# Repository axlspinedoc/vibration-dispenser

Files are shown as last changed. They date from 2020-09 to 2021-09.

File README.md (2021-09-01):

<h3 align="center">Dispensador Vibratorio</h3>

<div align="center">

[]()

</div>

---

<p align="center"> Automatización de un equipo dispensador de alimentos a granel
    <br> 
</p>

# 🧐 Acerca del proyecto 

Este repositorio contiene el código fuente del sistema operativo de una dispensador a granel utilizando un microcontrolador Amega2560

# 🏁 Preparación necesaria 

1. Instale la herramienta [VSCode](https://code.visualstudio.com)

2. Abra el programa y entre a _File_, _Preferences_, _Extensions_.

3. En el buscador, introduzca _C/C++_ e instale la extensión.

4. Nuevamente en el buscador, introduzca ahora _PlatformIO IDE_ e instale.

5. Una vez instalados correctamente, cada vez que abra VSCode aparecerá la pantalla de inicio con el anuncio "Welcome to PlatformIO"

6. Descargue una copia de este repositorio desde la opción _Code_, _Descargar Zip_. Descomprima en una ubicación conocida.

7. Desde la pestaña de _home_ de PlatformIO, seleccione _import Arduino project_

8. El programa cargara el proyecto y actualizará los documentos dependiendo la computadora donde se abra. *Espere 5 minutos*, esto permitirá que esté listo para programar

9. Para verificar que está listo busque el botón _Build_ en la barra inferior azul, marcado con el símbolo de palomilla

10. Si en el panel inferior aparece la instrucción [SUCCESS], está listo para programar. Conecte el Arduino a su computadora con el cable USB

11. Presione el botón _Upload_ en la barra inferior azul, marcado con una flecha hacia la derecha. Este botón está inmediatamente a la derecha del botón con la palomilla.

12. Pasados 15 segundos, el _Arduino_ se habrá reinicializado. ¡Ha actualizado exitosamente su microcontrolador!

# Para realizar Ajustes

Abra el archivo _utilities.h_ dentro de la carpeta _lib/inc_

Desde aquí puede editarse:

1. Producto a cargar al iniciar el equipo
2. Peso inicial default
3. Tiempo de espera cuando termina de vaciarse la Tolva
4. Selección del modo del relevador
5. Posiciones de la puerta en el estado ABIERTO y CERRADO
6. Sensibilidad de la báscula durante dispensado y vaciado
7. Calibración de báscula
8. Tiempo de señal de _Relay_
9. Tiempo de espera después de dispensar en tolva

Para editar la base de datos de productos abra el archivo _productos.h_ dentro de la carpeta _lib/inc_

Siga las indicaciones del archivo para agregar productos seleccionables desde la pantalla

# ⛏️ Built Using 

- [Visual Studio Code](https://code.visualstudio.com) - IDE
- [PlatformIO](https://platformio.org) - Embedded development IDE
- [Arduino Mega](https://www.arduino.cc) - Prototyping

# ✍️ Authors 

- [@axlspinedoc](https://github.com/axlspinedoc) - Developer

# 🎉 Acknowledgements 

- Amber Macias

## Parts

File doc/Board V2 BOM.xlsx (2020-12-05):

Costo de material por unidad | $938.00
Elemento | Cantidad | Costo Unitario | Costo final | Link
Pantalla LCD 16x2 | 1 | $60.00 | $60.00 | https://troxino.com/collections/pantallas/products/pantalla-lcd-caracteres-16x2-fondo-azul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
Arduino Mega genérico | 1 | $325.00 | $325.00 | https://troxino.com/products/arduino-mega-2560-generico?_pos=2&_sid=26eb9a378&_ss=r
Manufactura PCB | 1 | $68.00 | $68.00 | https://jlcpcb.com
Módulo 4 Relays | 1 | $70.00 | $70.00 | https://troxino.com/products/modulo-de-relevadores-4-canales-5v?_pos=4&_sid=eee105e99&_ss=r
Adaptor I2C para LCD | 1 | $45.00 | $45.00 | https://troxino.com/products/pantalla-lcd-caracteres-16x2-con-interfaz-i2c-integrada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
Tira sencilla 36 Pines | 2 | $8.00 | $16.00 | https://www.steren.com.mx/tira-sencilla-de-36-pines-para-circuitos-impresos.html
Regulador 5V para Servo | 1 | $9.00 | $9.00 | https://www.steren.com.mx/regulador-de-voltaje-positivo-5v-1a.html
Capacitor electrolítico 2.2uF | 2 | $3.00 | $6.00 | https://www.steren.com.mx/capacitor-electrolitico-radial-de-2-2-uf-micro-faradios-a-63-volts.html
Paquete de 10 resistencias 10K ohms | 1 | $10.00 | $10.00 | https://troxino.com/collections/resistencias/products/10-resistencias-4-7k-ohms-1-4-watts-1
Módulo driver para motor DC LD298 | 1 | $65.00 | $65.00 | https://troxino.com/products/puente-h-doble-l298n?variant=17821544415332
Servo Motor MG995 | 1 | $110.00 | $110.00 | https://troxino.com/products/servomotor-mg995?_pos=1&_sid=a9c5e8dc2&_ss=r
Boton pulsador rojo | 7 | $22.00 | $154.00 | http://semty.mx/index.php?id_product=867&controller=product
Regulador 120VAC a 12VD | 1 | $0.00 | $0.00
Header con clavija x2 pines | 2 | $0.00 | $0.00
Header con clavija x3 pines | 5 | $0.00 | $0.00
Header con clavija x4 pines | 4 | $0.00 | $0.00

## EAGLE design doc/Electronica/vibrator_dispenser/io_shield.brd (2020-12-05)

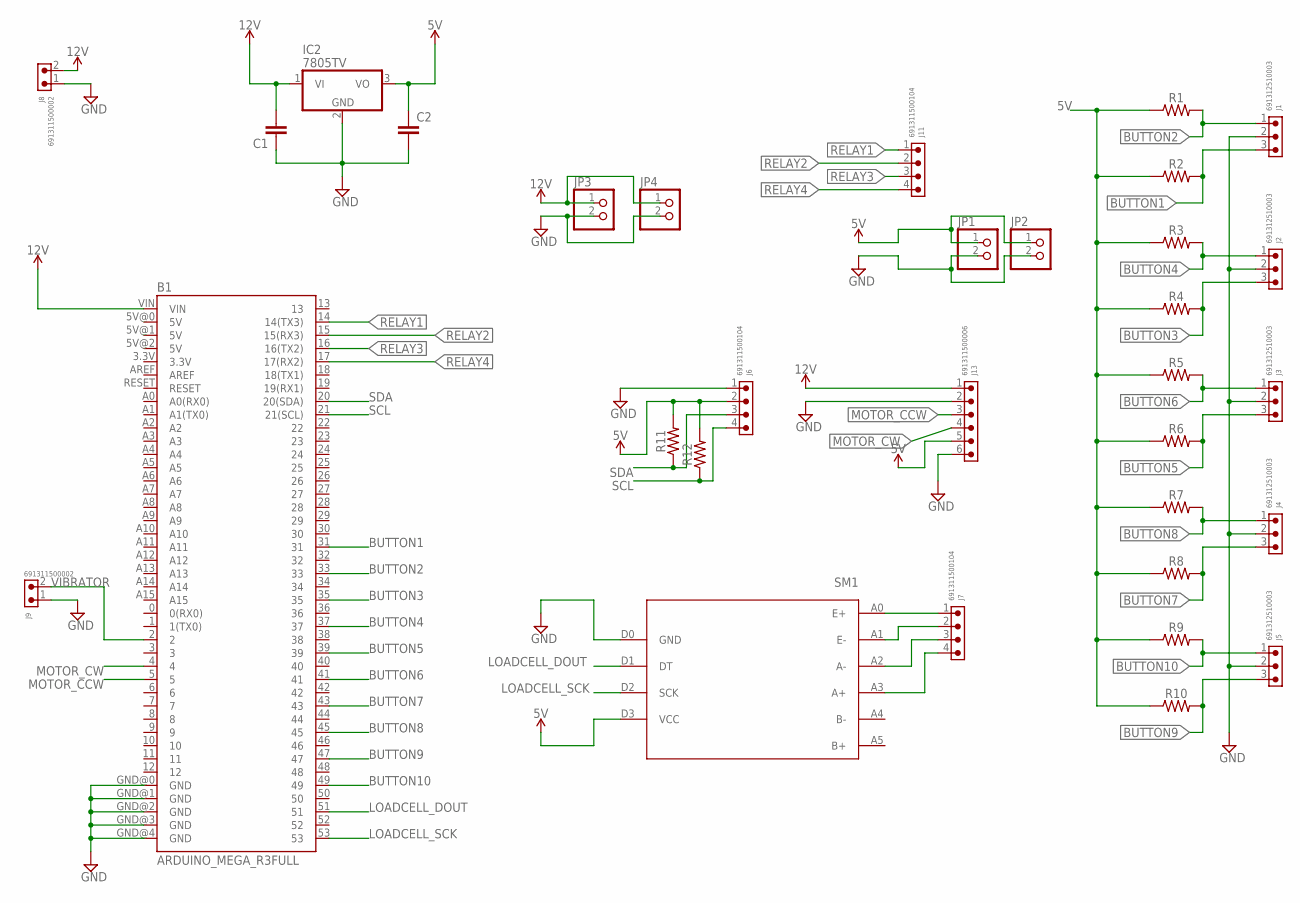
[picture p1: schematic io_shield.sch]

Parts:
B1: ARDUINO_MEGA_R3FULL; ARDUINO_MEGA
C1, C2: C-EU050-025X075; C050-025X075
IC2: 7805TV; TO220V
J1, J2, J3, J4, J5: 691312510003
J6, J7, J11: 691311500104
J8, J9: 691311500002
J13: 691311500006
JP1, JP2, JP3, JP4: PINHD-1X2; 1X02
R1, R2, R3, R4, R5, R6, R7, R8, R9, R10, R11, R12: AXIAL-0.3
SM1: HX711

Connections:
5V: C2.1, IC2.3 (VO), J6.2, J13.5, JP1.1, JP2.1, R1.P$1 (1), R2.P$1 (1), R3.P$1 (1), R4.P$1 (1), R5.P$1 (1), R6.P$1 (1), R7.P$1 (1), R8.P$1 (1), R9.P$1 (1), R10.P$1 (1), R11.P$2 (2), R12.P$2 (2), SM1.D3 (VCC)
12V: B1.VIN, C1.2, IC2.1 (VI), J8.2, J13.1, JP3.1, JP4.1
A+: J7.4, SM1.A3 (A+)
A-: J7.3, SM1.A2 (A-)
BUTTON1: B1.31, J1.3, R2.P$2 (2)
BUTTON2: B1.33, J1.1, R1.P$2 (2)
BUTTON3: B1.35, J2.3, R4.P$2 (2)
BUTTON4: B1.37, J2.1, R3.P$2 (2)
BUTTON5: B1.39, J3.3, R6.P$2 (2)
BUTTON6: B1.41, J3.1, R5.P$2 (2)
BUTTON7: B1.43, J4.3, R8.P$2 (2)
BUTTON8: B1.45, J4.1, R7.P$2 (2)
BUTTON9: B1.47, J5.3, R10.P$2 (2)
BUTTON10: B1.49, J5.1, R9.P$2 (2)
E+: J7.1, SM1.A0 (E+)
E-: J7.2, SM1.A1 (E-)
GND: B1.GND@0 (GND), B1.GND@1 (GND), B1.GND@2 (GND), B1.GND@3 (GND), B1.GND@4 (GND), C1.1, C2.2, IC2.2 (GND), J1.2, J2.2, J3.2, J4.2, J5.2, J6.1, J8.1, J9.1, J13.2, J13.6, JP1.2, JP2.2, JP3.2, JP4.2, SM1.D0 (GND)
LOADCELL_DOUT: B1.51, SM1.D1 (DT)
LOADCELL_SCK: B1.53, SM1.D2 (SCK)
MOTOR_CCW: B1.5, J13.3
MOTOR_CW: B1.4, J13.4
RELAY1: B1.14 (14(TX3)), J11.1
RELAY2: B1.15 (15(RX3)), J11.2
RELAY3: B1.16 (16(TX2)), J11.3
RELAY4: B1.17 (17(RX2)), J11.4
SCL: B1.21 (21(SCL)), J6.4, R12.P$1 (1)
SDA: B1.20 (20(SDA)), J6.3, R11.P$1 (1)
VIBRATOR: B1.2, J9.2

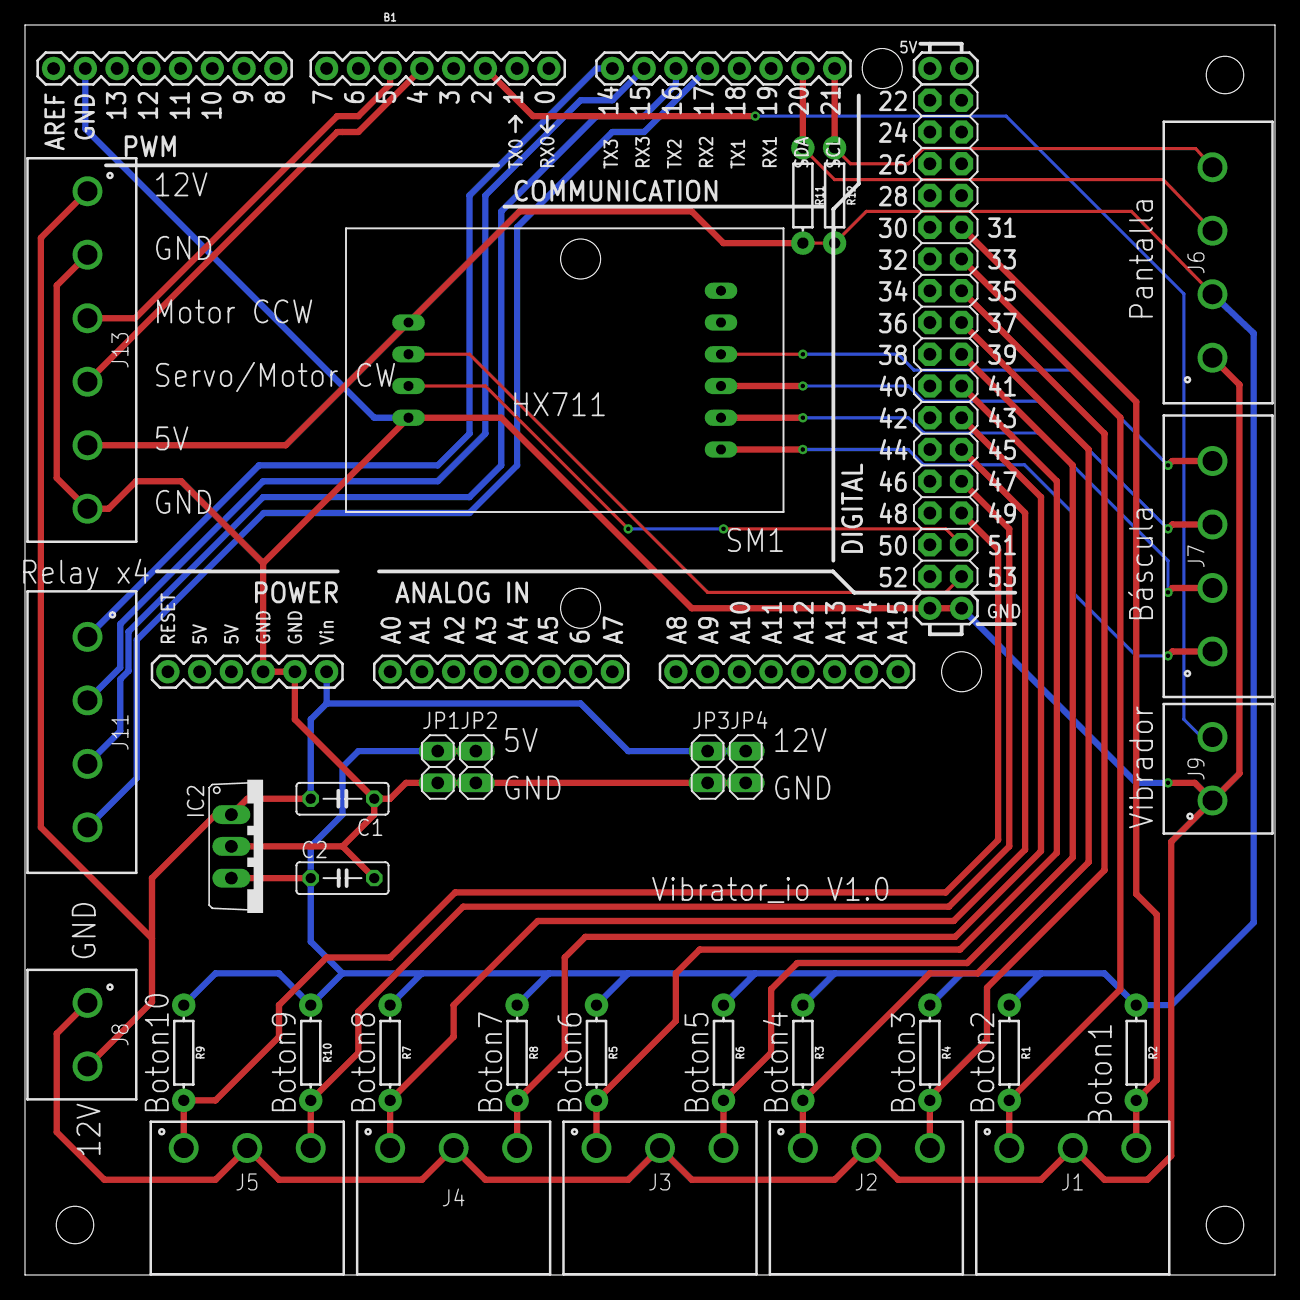
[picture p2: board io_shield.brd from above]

Board: 2 copper layers, 100.0 x 100.0 mm, 32 parts (0 on the bottom side), 28 nets.

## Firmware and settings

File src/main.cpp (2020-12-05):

//------------------------------------------------------------------------------
// @file: main.cpp
// @author: Axel Sandoval
// @e-mail: axel_isc@hotmail.com
// @created on: September 15, 2020
// 
//
// @brief: Source code for a vibration dispenser machine with scalability.
// LICENCE
//------------------------------------------------------------------------------

#include <Arduino.h>
#include <Servo.h>
#include "../lib/inc/utilites.h"
#include "../lib/state_machine/state_machine.h"
#include "../lib/io/button.h"
#include "../lib/scale/HX711.h"
#include "../lib/io/screencom.h"
#include "../lib/io/keypad.h"
#include "../lib/MHAdapter/LiquidCrystal_I2C.h"
#include "../inc/productos.h"

using namespace vibration_dispenser;

control::State_machine machine_state;
io::Button disp_button(DISPENSE_BUTTON_PIN,100);
io::Button cancel_button(CANCEL_BUTTON_PIN,100);
io::Button up_button(UP_BUTTON_PIN,100);
io::Button right_button(RIGHT_BUTTON_PIN,100);
io::Button down_button(DOWN_BUTTON_PIN,100);
io::Button left_button(LEFT_BUTTON_PIN,100);
io::Button enter_button(ENTER_BUTTON_PIN,100);

HX711 scale;

#ifdef MODO_SERVO
Servo door_servo;
#endif

LiquidCrystal_I2C lcd(0x3F, 16, 2);

// Serial comm DEBUGGING
char incomingChar;

// Process variables
int weight=PESO_DEFAULT;
int read_weight=0;
int previous_read_weight=0;
unsigned long previous_weight_timestamp=0;
int new_weight;
int progress=0;
int door_delay=TIEMPO_ESPERA*1000;
uint16_t relay_delay=TIEMPO_DE_RELAY*1000;
int delay_after_dispense=TIEMPO_DESPUES_DISP*1000;
unsigned long previous_buzzer_timestamp=0;
bool buzzer_on = false;
int served_weight=0;
bool wrong_weight = false;
unsigned long timer_alarma=0;

int new_first_speed;
int new_second_speed;
int new_speed_change_percentage;
int speed;
int menu=0;
int product_id=PRODUCTO_INICIAL;
int new_product_id=PRODUCTO_INICIAL;
int first_speed=product_param[product_id][0];
int second_speed=product_param[product_id][1];
int speed_change_percentage=product_param[product_id][2];

// Forward definitions of Screencom
Key checkArrowButtons();
void resetArrowButtons();
void setScreen(Screen menu, int old_weight_=0, int new_weight_=0);
void splashScreen();
void standbyScreen();
void dispensingScreen();
void servedScreen(int servido);
void openDoorScreen();
void setWeightScreen(int old_weight_, int new_weight_, int col = 14);
void setSpeedScreen(int old_value_,int new_value_, int col = 14);
void changeConfirmedScreen();
void errorScreen(String msg);
int manageWeight(int saved_weight);
int manageSpeed(int saved_speed);
int manageProduct(int saved_product);
void setProductScreen();
void standbyMenus(int menu_num);

// Forward definitions of vibrator
void setVibration(int percentage);

// Forward definition for reading scale
int readScale(unsigned long timestamp, int prev_value);
// Forward definition for buzzer relay
void buzzer(unsigned long timestamp, unsigned long frecuencia);

void setup() {
  
  Serial.begin(115200);
  Serial.println("System initialized");
  
  #ifdef MODO_SERVO
  door_servo.attach(SERVO_PIN);
  door_servo.write(DOOR_CLOSED);
  #endif
  
  #ifdef MODO_MOTOR
  pinMode(DC_CCW_PIN,OUTPUT);
  pinMode(DC_CW_PIN,OUTPUT);
  #endif

  #ifdef MODO_MOTOR
  analogWrite(DC_CCW_PIN,VELOCIDAD_CIERRE);
  analogWrite(DC_CW_PIN,0);
  #endif

  scale.begin(LOADCELL_DOUT_PIN, LOADCELL_SCK_PIN);  
  
  //if (scale.wait_ready_retry(20,100))  
  if (scale.is_ready())
  {    
    scale.set_scale(SCALE_GRAMS);
    scale.tare();
  }else{
    // This should be an Error condition
    Serial.println("Scale not detected");
  }
    
  // Screencom
  lcd.begin();
  setScreen(Screen::SPLASH);
  delay(500);
  machine_state.setState(control::State::STANDBY);
  setScreen(Screen::STANDBY);  
  
  // Vibrator
  pinMode(VIBRATOR_PIN, OUTPUT);

  // Relays
  pinMode(RELAY1_PIN,OUTPUT); // Vibrador para Tolva
  pinMode(RELAY2_PIN,OUTPUT); // Alarma
  pinMode(RELAY3_PIN,OUTPUT); // Chicharra
  pinMode(RELAY4_PIN,OUTPUT); // --Libre--
  
  // Relay behavior is inverted
  digitalWrite(RELAY1_PIN,HIGH);
  digitalWrite(RELAY2_PIN,HIGH);
  digitalWrite(RELAY3_PIN,HIGH);
  digitalWrite(RELAY4_PIN,HIGH);

}

void loop() {
    
  if (Serial.available()>0)
  {
    if (Serial.available()==1)
    {
      // Single key: Next Stage
      incomingChar=Serial.read();
    }    
  }
  
    switch (machine_state.getState())
    {
    case control::State::STANDBY:
      disp_button.update();
      cancel_button.update();
      
      if (cancel_button.getState())
      {
        cancel_button.reset();
        machine_state.setState(control::State::SERVED);
        lcd.clear();
        lcd.print("|  Vaciando... |");
      }
            

      //Menu scroller            
      switch (checkArrowButtons())
      {
      case Key::UP:
        resetArrowButtons();
        if (menu==6)
        {
          menu=0;
          standbyMenus(menu);
        }else
        {
          ++menu;
          standbyMenus(menu);                  
        }                
        break;
      case Key::DOWN:
        resetArrowButtons();
        if (menu==0)
        {
          menu=6;
          standbyMenus(menu);
        }else{
          --menu;
          standbyMenus(menu);        
        }
        break;
      
      case Key::SELECT:
        if (menu!=0)
        {
          switch (menu)
          {
          case 1:
            resetArrowButtons();
            machine_state.setState(control::State::TARE);
            Serial.println("State:= TARE");
            break;
          case 2:
            resetArrowButtons();
            machine_state.setState(control::State::SETGRAMS);
            Serial.println("State:= SETGRAMS");
            setScreen(Screen::SETWEIGHT,weight,weight);
            break;
          case 3:
            resetArrowButtons();
            machine_state.setState(control::State::SETSPEED1);
            Serial.println("State:= SETSPEED1");
            setScreen(Screen::SETSPEED1,first_speed,first_speed);
            break;
          case 4:
            resetArrowButtons();
            machine_state.setState(control::State::SETSPEED2);
            Serial.println("State:= SETSPEED2");
            setScreen(Screen::SETSPEED1,second_speed,second_speed);
            break;
          case 5:
            resetArrowButtons();
            machine_state.setState(control::State::SETSPEEDCHANGE);
            Serial.println("State:= SETSPEEDCHANGE");
            setScreen(Screen::SETSPEED1,speed_change_percentage,speed_change_percentage);
            break;
          case 6:
            resetArrowButtons();
            machine_state.setState(control::State::SETPRODUCT);
            Serial.println("State:= SETPRODUCT");
            setScreen(Screen::SETPRODUCT);
            break;
          
          default:
            break;
          }
        }        
        break;
      
      default:
        break;
      }
      
      if(incomingChar=='D' || disp_button.getState()){
        disp_button.reset();
        incomingChar='.';
        machine_state.setState(control::State::DISPENSING);        
        Serial.println("State:= DISPENSING"); 
        setScreen(Screen::DISPENSING);
        speed=first_speed;
        Serial.print("Speed:= ");
        Serial.println(speed);                            
      }     
      break;
    
    case control::State::TARE:      
      scale.tare();
      lcd.clear();
      lcd.print("| Bascula en 0 |");
      delay(1000);
      menu=0;
      standbyMenus(menu);
      machine_state.setState(control::State::STANDBY);
      Serial.println("State:= STANDBY");
      setScreen(Screen::STANDBY);
      break;
    
    case control::State::SETGRAMS:

      new_weight=manageWeight(weight);      
      if (new_weight!=weight)
      {
          weight=new_weight;
          changeConfirmedScreen();
          Serial.println(weight);
      }            
      machine_state.setState(control::State::STANDBY);
      Serial.println("State:= STANDBY");
      setScreen(Screen::STANDBY);
      menu=0;

      break;

    case control::State::SETSPEED1:
      
      new_first_speed=manageSpeed(first_speed);      
      if (new_first_speed!=first_speed)
      {
          first_speed=new_first_speed;          
          changeConfirmedScreen();
          Serial.println(first_speed);
      }

      menu=0;
      standbyMenus(menu);
      machine_state.setState(control::State::STANDBY);
      Serial.println("State:= STANDBY");
      setScreen(Screen::STANDBY);
      break;

    case control::State::SETSPEED2:
      
      new_second_speed=manageSpeed(second_speed);      
      if (new_second_speed!=second_speed)
      {
          second_speed=new_second_speed;          
          changeConfirmedScreen();
          Serial.println(second_speed);
      }
      
      menu=0;
      standbyMenus(menu);
      machine_state.setState(control::State::STANDBY);
      Serial.println("State:= STANDBY");
      setScreen(Screen::STANDBY);
      break;

    case control::State::SETSPEEDCHANGE:
      
      new_speed_change_percentage=manageSpeed(speed_change_percentage);      
      if (new_speed_change_percentage!=speed_change_percentage)
      {
          speed_change_percentage=new_speed_change_percentage;          
          changeConfirmedScreen();
          Serial.println(speed_change_percentage);
      }
      menu=0;
      standbyMenus(menu);
      machine_state.setState(control::State::STANDBY);
      Serial.println("State:= STANDBY");
      setScreen(Screen::STANDBY);
      break;
    
    case control::State::SETPRODUCT:
      
      new_product_id=manageProduct(product_id);      
      if (new_product_id!=product_id)
      {
          product_id=new_product_id;          
          first_speed=product_param[product_id][0];
          second_speed=product_param[product_id][1];
          speed_change_percentage=product_param[product_id][2];          
          changeConfirmedScreen();
          Serial.println(product_id);
      }
      
      menu=0;
      standbyMenus(menu);
      machine_state.setState(control::State::STANDBY);
      Serial.println("State:= STANDBY");
      setScreen(Screen::STANDBY);
      break;

    case control::State::DISPENSING:
      
      cancel_button.update();
      setVibration(speed);
      // TODO: Add "scale.is_ready() for protection and avoid hanging"
      if (scale.read() < 8000000)
      {                
        read_weight = readScale(millis(), read_weight);
        progress= (int)(((float)read_weight/weight)*100);        
        Serial.print("progreso: ");
        Serial.println(progress);
        
        if (progress>=speed_change_percentage || (weight<=100))
        {
          speed=second_speed;
          Serial.print("Speed:=");
          Serial.println(speed);
        }
        

      } else {
        speed=0;
        setVibration(speed);
        machine_state.setState(control::State::ERROR);
        Serial.println("State:= ERROR");
        errorScreen("Falla en bascula");        
        break;
      }
                  
      // TODO: Send to Screencom to update weight
      lcd.setCursor(0,1);
      lcd.print("                ");
      lcd.setCursor(0,1);      
      lcd.print(read_weight);
      lcd.print("/");
      lcd.print(weight);
      lcd.print("g");
      
      // Door button used as cancel
      if ((read_weight>=weight) || cancel_button.getState())      
      {        
        cancel_button.reset();
        speed=0;
        setVibration(speed);
        progress=0;        
                
        delay(500);
        // Change: SERVED Screen now shows quantity dispensed
        served_weight = scale.get_units(SENSIBILIDAD_VACIADO);
        setScreen(Screen::SERVED, served_weight);
        if ((served_weight-ERROR_PERMISIBLE)>weight || (served_weight+ERROR_PERMISIBLE) < weight)
        {
          wrong_weight=true;
          Serial.println("Wrong weight");
        }else
        {
          wrong_weight=false;
          Serial.println("Correct weight");
        }        
        
        Serial.println("State:= SERVED");
        
        // From here, we will delay 2s and jump right into FLUSH
        delay(delay_after_dispense);                
        digitalWrite(RELAY1_PIN,LOW);
                        
        machine_state.setState(control::State::SERVED);        

      }
      break;  

    case control::State::SERVED:
        
        // In case we arrive here, jump to FLUSH        
        machine_state.setState(control::State::FLUSH);        
        #ifdef MODO_SERVO
        door_servo.write(DOOR_OPEN);      
        #endif

        #ifdef MODO_MOTOR
        analogWrite(DC_CCW_PIN,0);
        analogWrite(DC_CW_PIN,VELOCIDAD_APERTURA);
        #endif

        setScreen(Screen::OPENDOOR);
      break;

    case control::State::FLUSH:      
      cancel_button.update();
      read_weight = readScale(millis(), read_weight);      
      
      // Show weight as it falls down to 0
      // First erase bottom row
      lcd.setCursor(0,1);
      lcd.print("                ");
      // Show how weight comes down to 0
      lcd.setCursor(4,1);
      lcd.print(read_weight);
      lcd.print(" g");
      
      // we leave cancel_button enabled in case door gets stuck open
      if ((read_weight < 15) || cancel_button.getState())
      {        
        cancel_button.reset();
        delay(door_delay);
        digitalWrite(RELAY1_PIN,HIGH);                
                                
        timer_alarma=millis();
        
        // Relevador para ALARMA
        digitalWrite(RELAY2_PIN,LOW);        
        while((millis()-timer_alarma)<relay_delay){
          
          if (wrong_weight==true)
          {            
            // Buzzer para mal peso          
            if ((millis()-timer_alarma)<relay_delay-800)            
                buzzer(millis(), FRECUENCIA_FALLA);                                              
          }
          else
          {
            // Buzzer para peso correcto
            if ((millis()-timer_alarma)<relay_delay-1800)            
              buzzer(millis(), FRECUENCIA_PASA);            
          }
                                        
        }
        digitalWrite(RELAY2_PIN,HIGH);
        digitalWrite(RELAY3_PIN,HIGH);
        buzzer_on=false;
        // erase flag
        wrong_weight=false;
        
        #ifdef MODO_SERVO
        door_servo.write(DOOR_CLOSED);
        #endif

        #ifdef MODO_MOTOR
        analogWrite(DC_CCW_PIN,VELOCIDAD_CIERRE);
        analogWrite(DC_CW_PIN,0);
        #endif
        
        machine_state.setState(control::State::STANDBY);        
        setScreen(Screen::STANDBY);
        Serial.println("State:= STANDBY");
        menu=0;
      }
      
      break;

    default: //Unknown State, shouldn't be reachable. Must prompt error.
        //machine_state.setState(control::State::ERROR);
        if (checkArrowButtons()==Key::SELECT)
        {
          incomingChar='.';
          digitalWrite(RELAY1_PIN,HIGH);
          digitalWrite(RELAY2_PIN,HIGH);
          digitalWrite(RELAY3_PIN,HIGH);
          digitalWrite(RELAY4_PIN,HIGH);
          resetArrowButtons();
          machine_state.setState(control::State::STANDBY);
          setScreen(Screen::STANDBY);
          break;
        }
              
      break;
    }  
}

//---------------------------------FUNCTIONS------------------------------------

// Forward definition for reading scale
int readScale(unsigned long timestamp, int prev_value){
  int ret = 0;
  if((timestamp - previous_weight_timestamp) > FRECUENCIA_BASCULA){
    ret = scale.get_units(SENSIBILIDAD_DISPENSADO);
    previous_weight_timestamp=millis();
  }else{
    ret = prev_value;
  }
  return ret;
}
// Forward definition for buzzer relay
void buzzer(unsigned long timestamp, unsigned long frecuencia){
  if ((timestamp - previous_buzzer_timestamp) > frecuencia)
  {
    if (buzzer_on==true)
    {
      digitalWrite(RELAY3_PIN, HIGH);
      buzzer_on = false;
    }else
    {
      digitalWrite(RELAY3_PIN, LOW);
      buzzer_on = true;
    }
    previous_buzzer_timestamp=millis();    
  }
  
}

Key checkArrowButtons(){
  
  up_button.update();
  right_button.update();
  left_button.update();
  down_button.update();
  enter_button.update();

  if(up_button.getState()==true){
    return Key::UP;
  }
  if(right_button.getState()==true){
    return Key::RIGHT;
  }
  if(left_button.getState()==true){
    return Key::LEFT;
  }
  if(down_button.getState()==true){
    return Key::DOWN;
  }
  if(enter_button.getState()==true){
    return Key::SELECT;
  } 
  return Key::NO_KEY;

}

void resetArrowButtons(){
  up_button.reset();
  right_button.reset();
  left_button.reset();
  down_button.reset();
  enter_button.reset();
}

void setScreen(Screen menu, int old_value_, int new_value_){
  if (menu!=Screen::SETWEIGHT)
  {
    lcd.noBlink();
  }
  
  switch (menu)
  {
  case Screen::SPLASH:
    splashScreen();
    break;
  case Screen::STANDBY:
    standbyScreen();
    break;    
  
  case Screen::SETSPEED1:
    setSpeedScreen(old_value_,new_value_);    
  break;
  
  case Screen::SETWEIGHT:
    setWeightScreen(old_value_,new_value_);
    break;
  case Screen::SETPRODUCT:
    setProductScreen();
    break;
  case Screen::DISPENSING:
    dispensingScreen();
    break;
  case Screen::SERVED:
    servedScreen(old_value_);
    break;
  case Screen::OPENDOOR:
    openDoorScreen();
    break;

  case Screen::ERRORSCREEN:
    //errorScreen();
    break;
  
  default:
    break;
  }
  
}  
void splashScreen(){
  lcd.clear();    
  lcd.setCursor(0,0);  
  lcd.print("Sistema iniciado");
  lcd.setCursor(11,1);
  lcd.print("V2.0");
  delay(250);
  lcd.clear();    
  lcd.setCursor(0,0);  
  lcd.print("|-----IDEA-----|");
  lcd.setCursor(0,1);
  lcd.print("|              |");
  delay(1000);

}
void standbyScreen(){  
  lcd.clear();
  lcd.setCursor(0,0);
  lcd.print(" Oprima 1 para  ");
  lcd.setCursor(0,1);
  lcd.print(" surtir ");
  lcd.print(weight);
  lcd.print("g");
}
void dispensingScreen(){
  lcd.clear();
  lcd.print("Dispensando...");
}
void servedScreen(int servido){
  lcd.clear();
  lcd.print("   Dispensado   ");   
  // screen mockup:
  // |   Dispensado   |
  // |     1000 g     |
  lcd.setCursor(4,1);
  lcd.print(servido);
  lcd.print(" g");
}
void openDoorScreen(){
  lcd.clear();
  // Only print static text on first row  
  lcd.print("   Vaciando...  "); 
}
void setWeightScreen(int old_weight_, int new_weight_, int col){
  lcd.clear();
  lcd.print("Peso prog.");
  lcd.setCursor(0,1);
  lcd.print("Nuevo peso");
  lcd.setCursor(15,0);
  lcd.print("g");
  lcd.setCursor(15,1);
  lcd.print("g");
  
  if (new_weight_<10)
  {        
    lcd.setCursor(14,1);
  }else if(new_weight_<100){    
    lcd.setCursor(13,1);
  }else if (new_weight_<1000){
    lcd.setCursor(12,1);
  } else {
    lcd.setCursor(11,1);
  }
  lcd.print(new_weight_);
  

  if (old_weight_<10)
  {        
    lcd.setCursor(14,0);
  }else if(old_weight_<100){    
    lcd.setCursor(13,0);
  }else if (old_weight_<1000){
    lcd.setCursor(12,0);
  } else {
    lcd.setCursor(11,0);
  }
  lcd.print(old_weight_);
  
  lcd.setCursor(col,1);
  lcd.blink();
}

// TODO: Change to Speed
void setSpeedScreen(int old_speed_, int new_speed_, int col){
  lcd.clear();
  lcd.print("Vel prog.");
  lcd.setCursor(0,1);
  lcd.print("Nueva Vel");
  
  if (new_speed_<10)
  {        
    lcd.setCursor(14,1);
  }else if(new_speed_<100){    
    lcd.setCursor(13,1);
  }else if (new_speed_<1000){
    lcd.setCursor(12,1);
  } else {
    lcd.setCursor(11,1);
  }
  lcd.print(new_speed_);
  

  if (old_speed_<10)
  {        
    lcd.setCursor(14,0);
  }else if(old_speed_<100){    
    lcd.setCursor(13,0);
  }else if (old_speed_<1000){
    lcd.setCursor(12,0);
  } else {
    lcd.setCursor(11,0);
  }
  lcd.print(old_speed_);
  
  lcd.setCursor(col,1);
  lcd.blink();
}



// Manages weight change screen. Allows user to change desired weight digit by
// digit.
int manageWeight(int saved_weight){
    
    int set_weight=saved_weight;
    int col=14;
    int increments[4] = {1,10,100,1000};    
    
    while (checkArrowButtons()!=Key::SELECT)
    {
        switch (checkArrowButtons())
        {
        case Key::RIGHT:              
            resetArrowButtons();                    
                if (col<14)
                {            
                    ++col;
                    lcd.setCursor(col,1);
                }        
            break;
        case Key::UP:              
            resetArrowButtons();        
            Serial.println("UP");
            set_weight += increments[14-col];
            if (set_weight>=2000)
            {
                set_weight=2000;
            }                        
            setWeightScreen(saved_weight,set_weight,col);
            break;
        case Key::DOWN:              
            resetArrowButtons();        
            Serial.println("DOWN");
            set_weight -= increments[14-col];
            if (set_weight<=0)
            {
                set_weight=0;
            }                        
            setWeightScreen(saved_weight,set_weight,col);
            break;
        case Key::LEFT:        
            resetArrowButtons();                            
                if (col>11)
                {            
                    --col;
                    lcd.setCursor(col,1);
                }
            break;        
        
        default:        
            break;
            }    
        }
    resetArrowButtons();
    return set_weight;       
}
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

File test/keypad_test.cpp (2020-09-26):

//------------------------------------------------------------------------------
// @file: button_test.cpp
// @author: Axel Sandoval
// @e-mail: axel_isc@hotmail.com
// @created on: September 15, 2020
// 
//
// @brief: Test code for Button library
// LICENCE
//------------------------------------------------------------------------------

#include <Arduino.h>
#include "../lib/inc/utilites.h"
#include "../lib/io/keypad.h"
#include "../lib/Keypad_shield/LiquidCrystal.h"


using namespace vibration_dispenser;

io::Keypad interface(KEYPAD_PIN);
LiquidCrystal lcd(pin_RS,  pin_EN,  pin_d4,  pin_d5,  pin_d6,  pin_d7);

void setup(){
  lcd.begin(LCD_COL,LCD_ROW);
  lcd.clear();      
  Serial.begin(115200);
  Serial.println("System ready");
}
void loop(){
           
            
    lcd.setCursor(0,0);    
    switch (interface.getKey())
    {
    case Key::RIGHT:              
        interface.resetKeys();
        lcd.print("Right ");
        delay(100);        // Only needed to retain char on lcd
        Serial.println("RIGHT");
        break;
    case Key::UP:              
        interface.resetKeys();
        lcd.print("Up    ");
        delay(100);        // Only needed to retain char on lcd
        Serial.println("UP");
        break;
    case Key::DOWN:              
        interface.resetKeys();
        lcd.print("Down  ");
        delay(100);        // Only needed to retain char on lcd
        Serial.println("DOWN");
        break;
    case Key::LEFT:        
        interface.resetKeys();
        lcd.print("Left  ");
        delay(100);        // Only needed to retain char on lcd
        Serial.println("LEFT");
        break;
    case Key::SELECT:        
        interface.resetKeys();
        lcd.print("Select");
        delay(100);        // Only needed to retain char on lcd
        Serial.println("SELECT");
        break;
    
    default:
        interface.resetKeys();
        lcd.print("  ..  ");
        break;
    }    
}
//----------------------END OF UNIT TEST----------------------------------------

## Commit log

2020-09-18 Added LCD functionality for MH LCDI2C Adapter, replaced previous library. TODO: Implement one time only LCD prints
    [main.cpp]
2020-09-19 Changed board to Arduino Mega
2020-09-19 Keypad shield and Arduino Mega fully functional
2020-09-20 WIP button library, broken atm
    [button_test.cpp, main.cpp]
2020-09-20 Changed button behavior
2020-09-20 Button library fully functional
2020-09-20 Implemented buttons to main. TODO Debug SERVED Stage
2020-09-20 Corrected button logic inside main. Buttons finalized
    [main.cpp]
2020-09-20 Changed tick() function to update() inside button to better reflect behavior
2020-09-24 Corrected keypad function. Keys are detectable now. TODO: Check debounce
    [keypad_test.cpp, main.cpp]
2020-09-25 Ready for PR, added scale.is_ready() to avoid hanging while working without scale
    [keypad_test.cpp, main.cpp]
2020-09-25 WIP manageWeight() redesigned setWeightScreen() to update set_weight continuously
    [main.cpp]
2020-09-25 Basic weight change functionality implemented. Some bugs still to correct
    [main.cpp]
2020-09-25 Preparing for vibrator. WIP function to transform decimal position to power of 10 in ints
    [main.cpp]
2020-09-26 Started implementation of PWM for vibration control. TODO: Add speed control
    [main.cpp]
2020-09-26 Added Scale disconnection detection during dispensing to avoid hanging
    [main.cpp]
2020-09-26 Added progress variable to track filling of funnel. WIP security for scale disconnection
2020-09-26 Added vibrator variation after set progress point
    [main.cpp]
2020-09-27 updated pins to PCB MVP
2020-09-28 Code of 1st functional prototype
2020-10-01 Speed changes applied. TODO: Test on board
2020-10-10 Inverted Servo
2020-10-13 [Bugfix] Product code was not shown on Menu tests. Changed displayed value
    [main.cpp]
2020-10-13 [Bugfix] Added missing resetKeys to manageProducts switch
    [main.cpp]
2020-10-13 [bugfix] Print currently loaded product at the start
    [main.cpp]
2020-10-13 Changed door_button logic to cancel button. At any time it can be pressed and will transfer to SERVED state
2020-10-13 Added pause configs for relay, served
2020-10-13 Fixed Relay delay time
    [main.cpp]
2020-12-03 Change LCD to I2C library and bus. Tests succesful
2020-12-03 Changed Keypad for io::Button objects. Compilation succesful
2020-12-04 Changed all pinouts to accomodate new vibrator_io V1.0 board
    [main.cpp]
2020-12-04 Integrated relays 1 and 2
2020-12-04 Debugged Relay module, relay ouputs are reversed
    [main.cpp]
2020-12-04 Device now knows when wrong weight was dispensed
    [main.cpp]
2020-12-05 Final code, Schematics and BOM integrated
    [Board V2 BOM.xlsx, io_shield.brd, io_shield.sch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]

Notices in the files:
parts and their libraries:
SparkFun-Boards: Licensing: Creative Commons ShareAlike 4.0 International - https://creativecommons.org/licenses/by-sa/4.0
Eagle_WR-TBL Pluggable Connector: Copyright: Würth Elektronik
